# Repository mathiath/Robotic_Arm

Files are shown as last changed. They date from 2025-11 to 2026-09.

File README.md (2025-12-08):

# Robotic Arm – HiØ Anvendt Robotteknikk (Fall 2025)

Firmware and serial communication interface for a 6-DOF robotic arm developed for the Applied Robotics course at Høgskolen i Østfold.

This code runs on a Teensy 4.1 and communicates with RoboDK through a Python bridge.

---

## Installing the Firmware
1. Install Arduino IDE.
2. Use the following instructions to add the Teensy 4.1 board to Arduino IDE: https://www.pjrc.com/teensy/td_download.html
3. Open `main.ino` in the Arduino IDE.
4. Select **Teensy 4.1** under Tools - Board.
5. Upload.

The file `serial.ino` is automatically detected and compiled by Arduino.

---

## Basic Usage

### 1. Startup Procedure

To ensure correct homing and encoder alignment:

1. Place the robot in the upright zero position (all joints at 0°)
2. Insert zeroing pins
3. Power the motor drivers
4. Connect USB to the Teensy, and wait for it to initialize and calibrate
5. Remove the pins before any movement is executed

### 2. Home Button

Pressing the HOME button moves the robot to the zero position for all joints.

### 3. FreeMove Mode

- The FreeMove button toggles the motor power.
- When FreeMove is active:
  - Motors are disabled.
  - The arm can be moved freely by hand, while still sending encoder-data to RoboDK

### 4. Serial Control

The controller accepts the following commands:

- `R[...]`  – set joint targets  
- `L<number>` – set robot speed  
- `E` – return current joint values  
- `G0` / `G1` – gripper off/on

---

## Emergency Stop (E-STOP)

- Pressing the E-STOP button immediately disables all motors. 
- The arm may fall freely depending on payload and joint position.

The E-STOP is a latching, dual-circuit safety stop:
- One circuit physically cuts the stepper driver ENABLE lines.
- The other provides a firmware-level stop for redundancy, and allows for future digital feedback to RoboDK.

The arm will not be operational until the E-STOP is manually unlatched and the system has been power-cycled and re-homed.

### Reset Procedure
1. Unplug the power to the arm and disconnect the USB cable
2. Unlatch the E-STOP button
3. Place the robot in the upright zero position
4. Insert zeroing pins
5. Reconnect motor power
6. Reconnect USB to the Teensy and wait for it to initialize and calibrate
7. Remove the pins before any movement is executed

---

## File Overview

- `main.ino` - Firmware: stepping, encoders, safety, button handling
- `serial.ino` - Serial parser used for RoboDK/Python communication 

Both files are compiled automatically by the Arduino IDE.

---

## Notes

- Current setup uses a single shared speed value for all joints, due to the RoboDK - Python interface.
- Acceleration smoothing is not implemented in this version.

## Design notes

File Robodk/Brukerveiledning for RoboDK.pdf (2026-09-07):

Brukerveiledning for RoboDK

Import av robotobjekt
For å sette opp simulering og etablere kommunikasjon mellom RoboDK og den fysiske roboten, må robotmodellen først legges inn i prosjektfilen. Dette gjøres ved å åpne RoboDK og utføre følgende:
1. Åpne en RoboDK-fil.
2. Gå til File → Open.
3. Velg robotmodellen av kalt: My-Mechanism.

Når robotobjektet er importert, må det konfigureres slik at alle parametere samsvarer med robotens virkelige spesifikasjoner.

Konfigurering av roboten
Høyreklikk på robotobjektet i RoboDK og velg Modify Robot.
Et nytt vindu åpnes, der alle innstillinger skal settes slik som angitt i referansebildet. Disse parameterne må stemme overens med robotens mekaniske og kinematiske data for at simuleringen skal være nøyaktig.

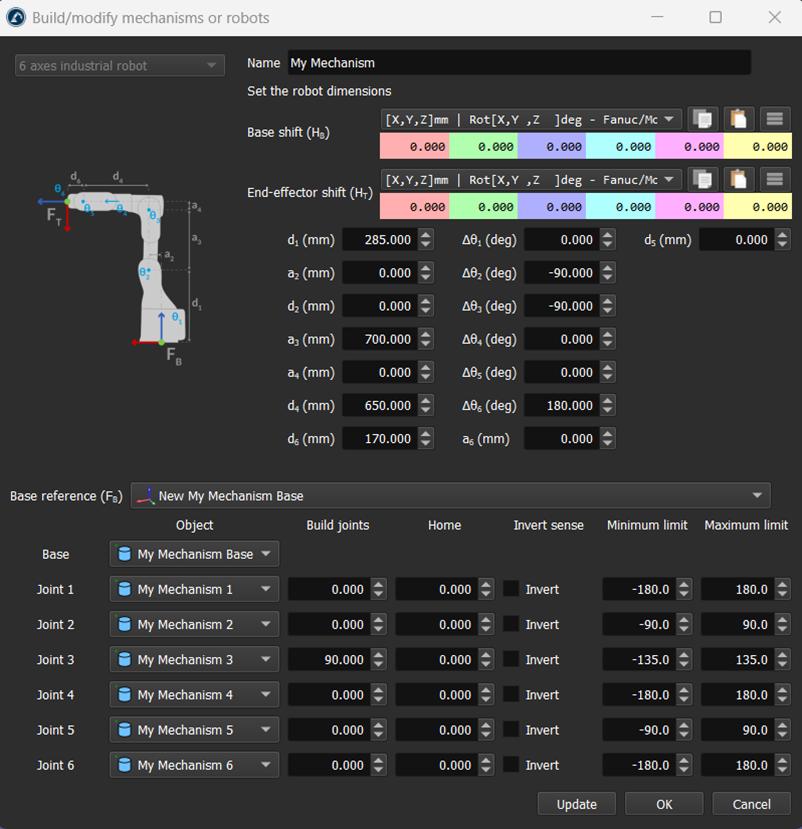
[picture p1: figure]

Når alle innstillinger samsvarer med spesifikasjonen, trykk Update og deretter OK.

Brukerveiledning for RoboDK

Plassering av robotbiblioteket
For at RoboDK skal kunne kommunisere med robotens bibliotek, må bibliotekfilen ligge i datamaskinens Temp-mappe. Dette kan gjøres på flere måter, men følgende metode er et effektivt alternativ (for Windows):
1. Opprett et nytt Python-script i RoboDK ved å høyreklikke i prosjektet og velge Add Python Script.
2. Høyreklikk deretter på scriptet og velg Edit Python Script.
3. I scriptvinduet, gå til File → Open/Open file.
4. RoboDK åpner da automatisk Temp-mappen på PC-en.
5. Legg robotbibliotekets fil i denne mappen.
Når biblioteket er plassert riktig, kan det brukes direkte av Python-skriptet.

Oppsett av Python-script for kommunikasjon
For å etablere kommunikasjon mellom roboten og RoboDK via Python, må klassen fra robotbiblioteket importeres.
Øverst i scriptet må følgende være definert:
- Import av robotens bibliotekklasse
- Opprettelse av et objekt av denne klassen
Dette objektet gjør det mulig å sende kommandoer og hente status fra roboten. Bilde under vise en eksempel kode som demonstrer bruken av objektet.

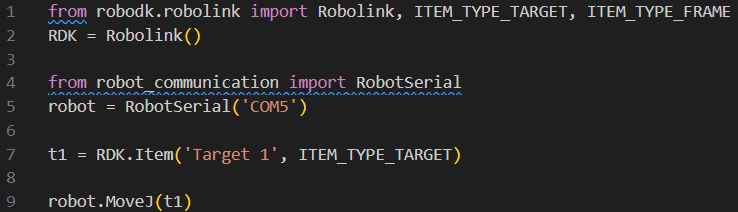
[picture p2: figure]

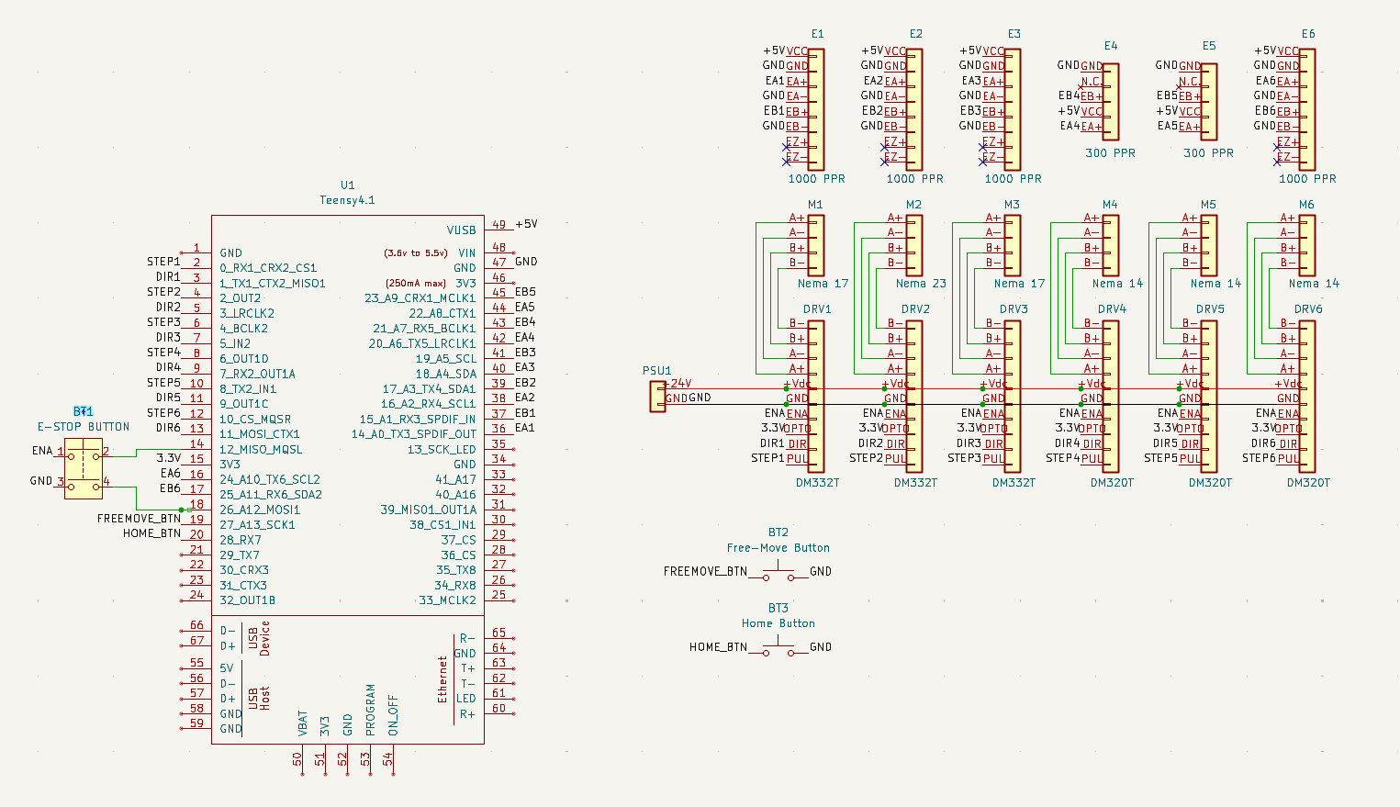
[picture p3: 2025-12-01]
schematic/robot_schematic.png

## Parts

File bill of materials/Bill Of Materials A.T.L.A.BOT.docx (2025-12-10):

# Bill Of Materials

PA12-GF15: ca 2,5kg uten feil.

https://polyalkemi.no/fiberlogy/101416/fiberlogy-nylon-pa12-plus-gf15-red

https://polyalkemi.no/fiberlogy/101413/fiberlogy-nylon-pa12-plus-gf15-black

PLA (for låsepinner)

da trenger vi også en hardened nozzle for å ikke ødelegge maskinen:

https://polyalkemi.no/bambu-lab/fah001-n-1/bambu-lab-hotend-for-p1-x1-hardened-steel-04mm

Tannhjul:

OBS, viktig med riktig dimensjoner og antall.

https://www.aliexpress.com/item/1005007667696756.html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

4x 20 teeth, 8mm bore

2x 28 teeth, 8mm bore

1x 40 teeth, 8mm bore

1x 30 teeth, 14mm bore

1x 40 teeth, 14mm bore

Encoderkabel:

CAT6 for encoder, skjermet, flerleder for fleksibilitet, 1stk.

https://www.avxperten.no/pds-kabel/s-ftp-cat6-bloed-100m-udendoers.asp

Kontakt for gripper: 1stk av hver

https://no.rs-online.com/web/p/industrial-circular-connectors/2088105

https://no.rs-online.com/web/p/sensor-actuator-cables/8566422

Mikrocontroller:

Teensy 4.1: https://www.amazon.com/gp/product/B08CTM3279?smid=A1283MCABFXB0Q&psc=1

Breakout board, screw mount: https://www.amazon.com/gp/product/B08R7P8G9X?smid=A2OVMUS055KMW5&psc=1

Hardware:

Diverse M3, M4, M5 og M6 maskinskruer, skiver og muttere

Ca 1m med 20x20 aluminiumsprofil gjerne av god kvalitet (stiv)

3mm svart MDF plate for kontrollerboks

Svart kabelsleeving

Tilfeldig bord fra skolen (med tillatelse)

Diverse strips

Kulelager:

Flatlager, 2stk:

https://www.123bearing.eu/bearing-housing/needle-roller-bearing/axial-needle/axk6085

Mellomstore lager, 4stk:

https://www.123bearing.eu/bearing-housing/deep-groove-bearing/single-row/61812-zz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

Store lager til base, 1stk:

https://www.123bearing.eu/bearing-housing/deep-groove-bearing/single-row/61928-2rs

Steppermotorer og girkasser:

1x https://www.omc-stepperonline.com/nema-17-closed-loop-stepper-motor-45ncm-64oz-in-with-magnetic-encoder-1000ppr-4000cpr-17hs15-1504-me1k

1x https://www.omc-stepperonline.com/eg-series-planetary-gearbox-gear-ratio-10-1-backlash-15-arc-min-for-nema-17-stepper-motor-eg17-g10

1x https://www.omc-stepperonline.com/nema-23-closed-loop-stepper-motor-1-20nm-169-93oz-in-with-magnetic-encoder-1000ppr-4000cpr-23hs22-4004-me1k

1x https://www.omc-stepperonline.com/eg-series-planetary-gearbox-gear-ratio-50-1-backlash-20-arc-min-for-6-35mm-shaft-nema-23-stepper-motor-eg23-g50-d6

1x https://www.omc-stepperonline.com/nema-17-closed-loop-stepper-motor-65ncm-92oz-in-with-magnetic-encoder-1000ppr-4000cpr-17hs24-2104-me1k

1x https://www.omc-stepperonline.com/eg-series-planetary-gearbox-gear-ratio-20-1-backlash-20-arc-min-for-nema-17-stepper-motor-eg17-g20

1x https://www.omc-stepperonline.com/nema-14-closed-loop-stepper-motor-40ncm-56-7oz-in-encoder-300cpr-14hs20-1504d-e22-300

3x https://www.omc-stepperonline.com/eg-series-planetary-gearbox-gear-ratio-20-1-backlash-20arc-min-for-nema-14-stepper-motor-egs14-g20

1x https://www.omc-stepperonline.com/nema-14-closed-loop-stepper-motor-18ncm-25-5oz-in-encoder-300cpr-14hs13-0804d-e22-300

1x https://www.omc-stepperonline.com/nema-14-closed-loop-stepper-motor-12-5ncm-17-73oz-in-with-magnetic-encoder-1000ppr-4000cpr-14hs11-1004-me1k

Stepper drivere:

4x (1 backup) https://www.omc-stepperonline.com/digital-stepper-drive-1-0-3-2a-18-30vdc-for-nema-17-23-stepper-motor-dm332t

4x (1 backup) https://www.omc-stepperonline.com/digital-stepper-driver-0-3-2-2a-10-30vdc-for-nema-8-11-14-16-17-stepper-motor-dm320t

Strømforsyning:

1x https://www.omc-stepperonline.com/400w-24v-16-7a-115-230v-switching-power-supply-stepper-motor-cnc-router-kits-s-400-24

Motorkabel:

15m: https://www.omc-stepperonline.com/awg-20-high-flexible-with-shield-layer-stepper-motor-cable-cm-20s

Elektriske småkomponenter:

Diverse jumper kabler

Wago klammer

2stk pushbuttons for homing og freemove

1stk låsende bryter for nødstopp

C13 apparatledning.

Micro-usb kabel

1x sikret bryter for 230v

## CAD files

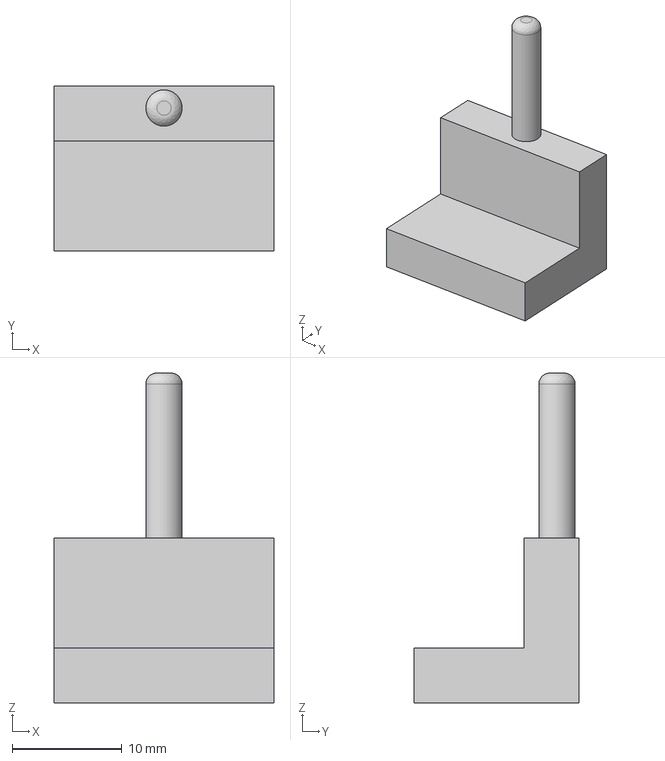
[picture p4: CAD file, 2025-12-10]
3D Models/locking_pin_joint6.step
20.0 x 15.0 x 30.0 mm

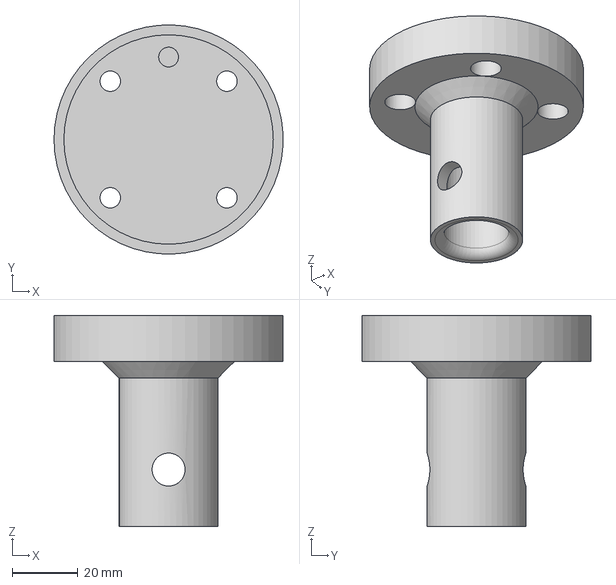
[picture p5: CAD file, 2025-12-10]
3D Models/tool_penholder.step
69.4 x 69.5 x 64.0 mm

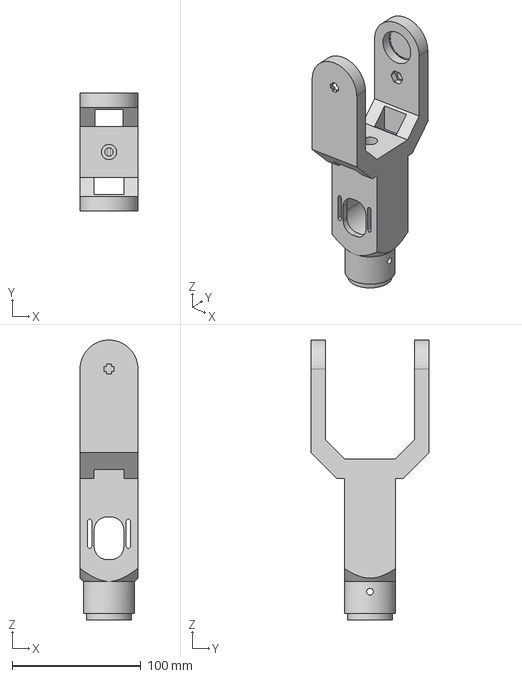
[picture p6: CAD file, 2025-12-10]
3D Models/fork_joint5_6.step
45.0 x 91.8 x 217.5 mm

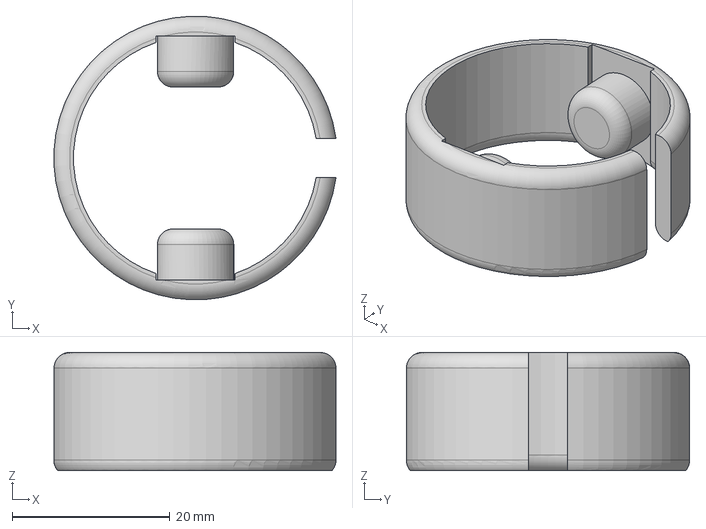
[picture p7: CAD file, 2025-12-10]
3D Models/tool_penholder_pressure_ring.step
35.8 x 36.0 x 15.0 mm

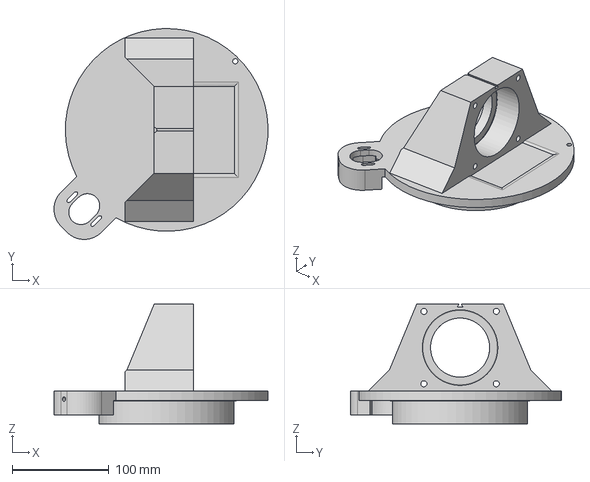
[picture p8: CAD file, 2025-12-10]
3D Models/base_top.step
221.7 x 218.4 x 124.0 mm

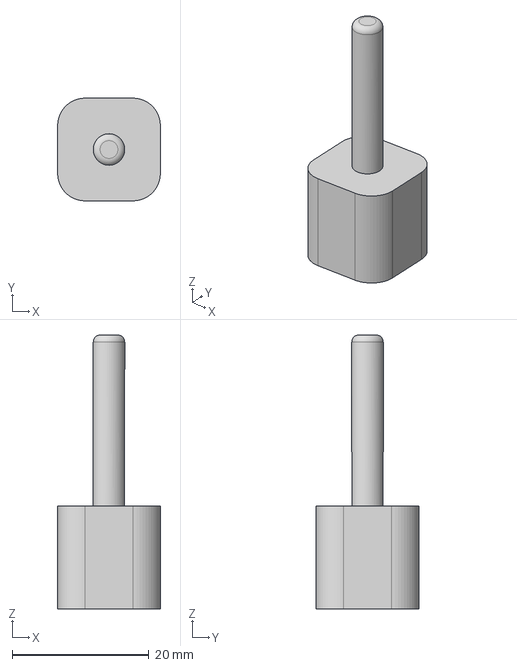
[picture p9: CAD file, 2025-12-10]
3D Models/locking_pin_joint1.step
15.0 x 15.0 x 40.0 mm

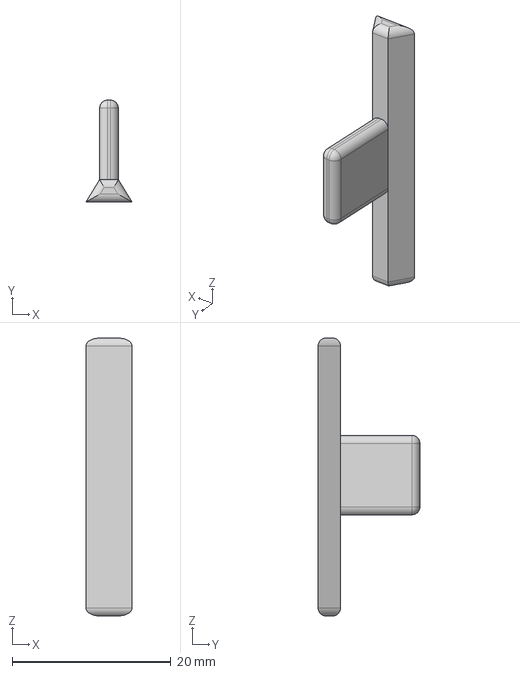
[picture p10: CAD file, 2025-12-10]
3D Models/locking_pin_joint2_3_4_might_need_some_scaling.step
5.80 x 12.8 x 35.0 mm

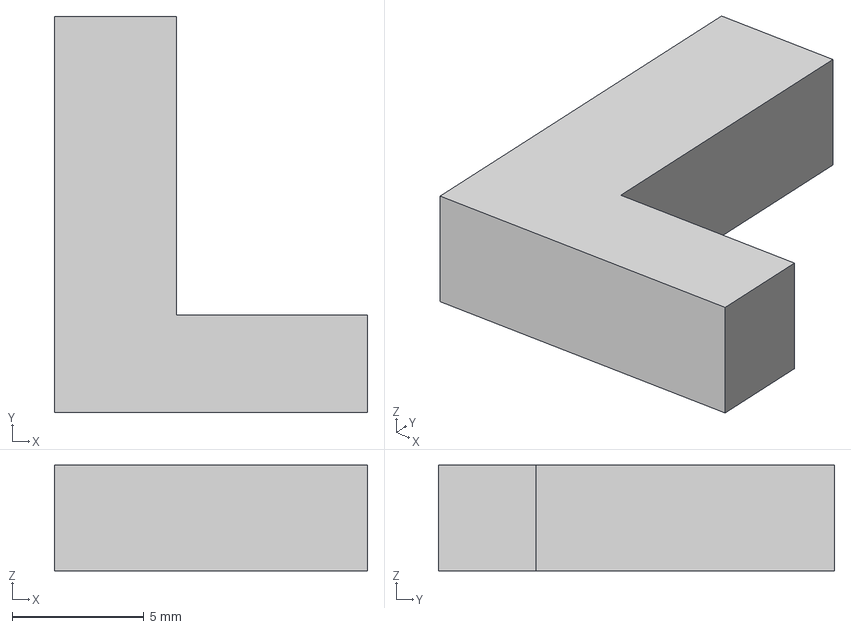
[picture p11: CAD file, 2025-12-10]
3D Models/letter_L.step
11.9 x 15.0 x 4.00 mm

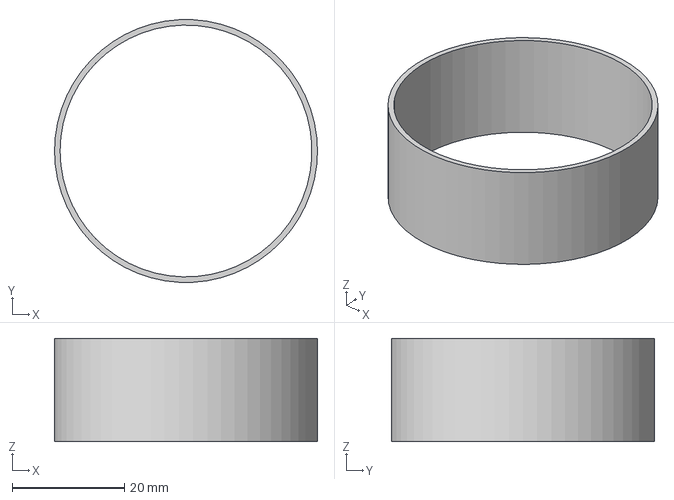
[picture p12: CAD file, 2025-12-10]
3D Models/joint4_middle_bearing_spacer.step
46.9 x 46.8 x 18.4 mm

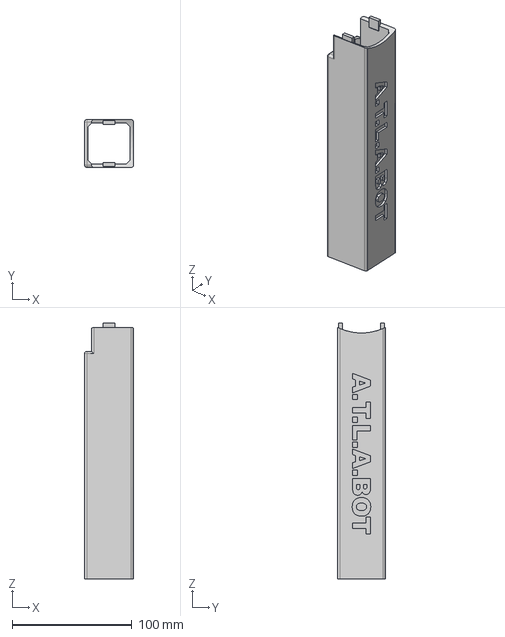
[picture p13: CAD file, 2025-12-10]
3D Models/upper_shroud_joint2-3.step
41.0 x 40.0 x 213.6 mm

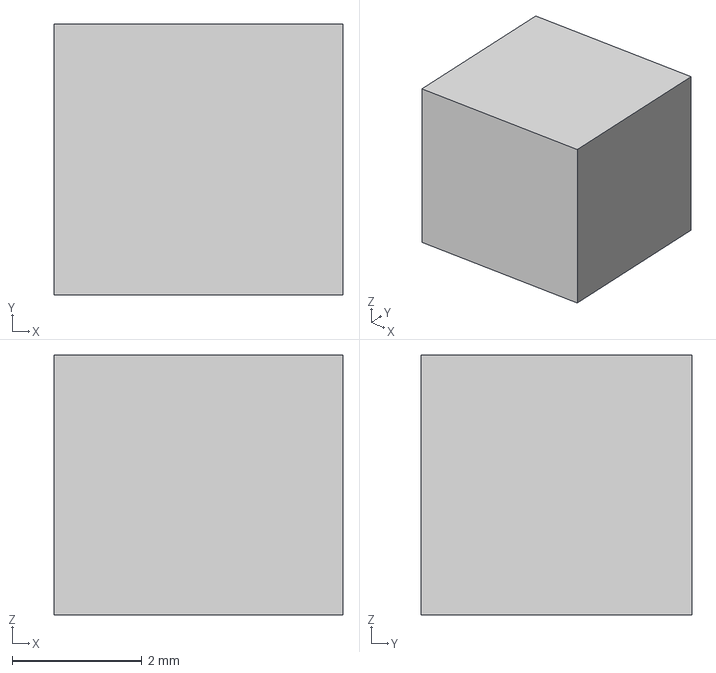
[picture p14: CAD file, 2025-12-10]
3D Models/letter_dot.step
4.45 x 4.17 x 4.00 mm

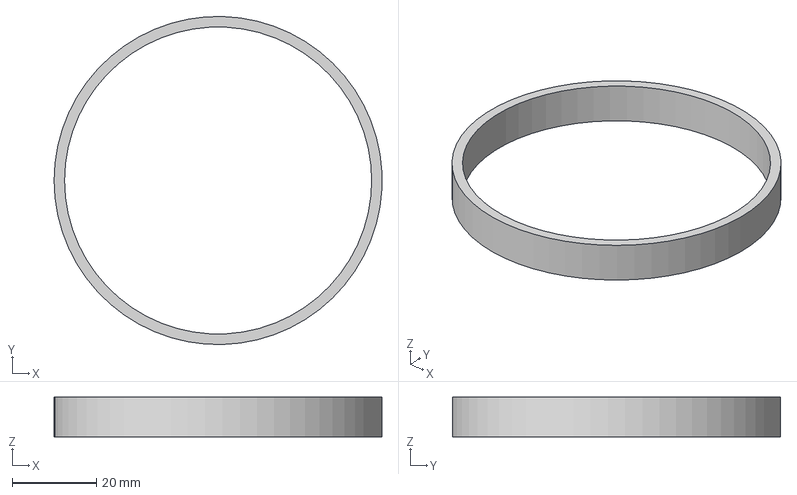
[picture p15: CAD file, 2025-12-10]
3D Models/joint2_3_bearing_spacer.step
77.9 x 78.0 x 9.50 mm

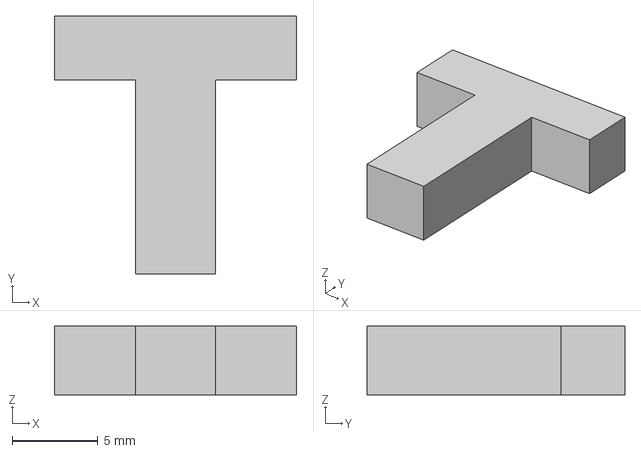
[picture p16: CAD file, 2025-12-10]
3D Models/letter_T.step
14.1 x 15.0 x 4.00 mm

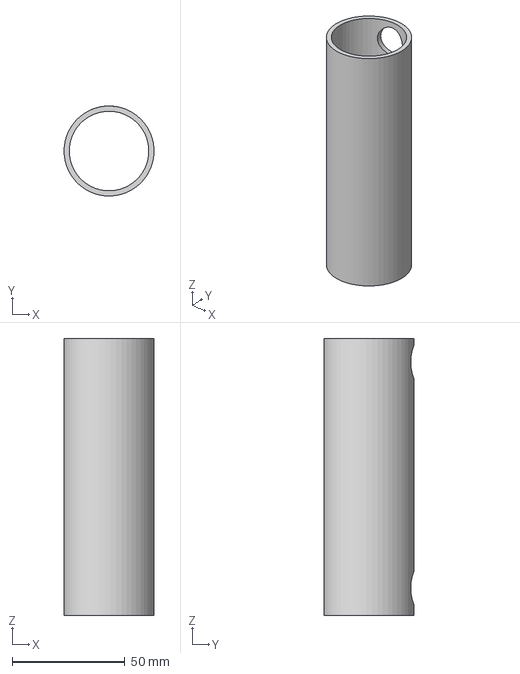
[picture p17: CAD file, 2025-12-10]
3D Models/upper_shroud_joint4_5.step
40.0 x 40.0 x 123.0 mm

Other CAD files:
3D Models/joint4_inner.step
3D Models/letter_A.step
3D Models/letter_B.step
3D Models/joint5_spacer.step
3D Models/CNC_cut_belt_pulley_T5_10T.f3d
3D Models/Elektronikkboks.f3d
3D Models/base_bottom.step
3D Models/joint2_inner.step
3D Models/joint2_motor_plate.step
3D Models/joint3_4_inner.step
3D Models/joint3_motor_plate.step
3D Models/joint3_outer.step
3D Models/joint4_outer_bearing_spacer_2pc.step
3D Models/joint5_6_housing.step
3D Models/joint6_outer.step
3D Models/letter_O.step
3D Models/locking_pin_joint5.step

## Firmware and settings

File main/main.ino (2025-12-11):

/* 
    Inspired by AR4 Robot Control Software
    Copyright (c) 2024, Chris Annin
    All rights reserved.

    This revision of the code has a shared speed for all joints during movement, due to the current RoboDK configuration only delivering one speed variable.

    To do: update gear ratios
*/

#include <Arduino.h>
#include <math.h>
#include <Encoder.h>

const int n_J = 6; // Number of joints

// external variables from RoboDK interface
extern float Jlist[6];
extern int robot_speed; // % of joint max deg/s

// pins
const int stepPin[n_J] = {0, 2, 4, 6, 8, 10};
const int dirPin[n_J]  = {1, 3, 5, 7, 9, 11};

const int encAPin[n_J] = {14, 16, 18, 20, 22, 24};
const int encBPin[n_J] = {15, 17, 19, 21, 23, 25};

const int enPin      = 12;
const int eStopPin   = 26; // latching button
const int freeMovePin= 27; // momentary button, yellow
const int homePin    = 28; // momentary button, green

// motor + encoder + driver specs
const int SPR = 1600; // motor steps per rev
const int CPR[n_J]       = {4000, 4000, 4000, 1200, 1200, 4000}; // encoder counts per rev
const float gearRatio[n_J] = {71,   50,   20,   20,   33.333,   20};   // gearbox ratio

const int invDir[n_J] = {0, 0, 0, 0, 0, 0}; // invert direction for motors

// encoder instances (one per joint)
Encoder enc[n_J] = {
    Encoder(encAPin[0], encBPin[0]),
    Encoder(encAPin[1], encBPin[1]),
    Encoder(encAPin[2], encBPin[2]),
    Encoder(encAPin[3], encBPin[3]),
    Encoder(encAPin[4], encBPin[4]),
    Encoder(encAPin[5], encBPin[5]),
};

// Joint limits (deg)
float limPos[n_J] = {180.0f,  90.0f,  135.0f, 360.0f,  90.0f,  360.0f};
float limNeg[n_J] = {-180.0f, -90.0f, -135.0f, -360.0f, -90.0f, -360.0f};

// Maximum velocity per joint (deg/s at 100% speed)
const float maxSpeed[n_J] = {30.0f, 20.0f, 30.0f, 40.0f, 30.0f, 180.0f};

const float accelK = 0.2f; // Acceleration duration (% of movement)
const float accelMinSpeed = 0.2f; // Percentage of speed at the acceleration's slowest point.

// internal vars
float encMult[n_J];  // encoder counts per degree (includes gearbox)
float stepDeg[n_J];  // motor steps per degree (includes gearbox)
long  encRaw[n_J];   // raw encoder counts
float encDeg[n_J];   // encoder deg position

long  stepCount[n_J]; // accumulated step count
float jointDeg[n_J];  // current joint angle (deg) from step count
long totalSteps[n_J]; // total steps for current move (for accel/decel)
long stepsDone[n_J];  // steps already taken in current move

// function state flags
bool motorsEnabled   = false;
bool eStopEnabled    = false;
bool freeMoveEnabled = false;

// init step/dir pins
void initPins() {
    pinMode(enPin, OUTPUT);
    pinMode(eStopPin, INPUT_PULLUP);
    pinMode(freeMovePin, INPUT_PULLUP);
    pinMode(homePin, INPUT_PULLUP);

    digitalWrite(enPin, LOW); // disable motors at startup
    
    // init all motor pins
    for (int j = 0; j < n_J; j++) {
        pinMode(stepPin[j], OUTPUT);
        pinMode(dirPin[j],  OUTPUT);
        digitalWrite(stepPin[j], LOW);
        digitalWrite(dirPin[j],  LOW);
    }
}

// init conversion parameters
void initParams() {
    for (int j = 0; j < n_J; j++) {
        encMult[j] = (float)(CPR[j] * gearRatio[j]) / 360.0f;
        stepDeg[j] = (float)(SPR   * gearRatio[j]) / 360.0f;
    }
}

// enable / disable motor drivers
void enableMotors(bool on) {
    motorsEnabled = on;
    digitalWrite(enPin, on ? HIGH : LOW);
}

// convert degrees to motor steps
long degToSteps(int joint, float deg) {
    if (joint < 0 || joint >= n_J) return 0;
    return lroundf(deg * stepDeg[joint]);
}

// convert motor steps to degrees
float stepsToDeg(int joint, long steps) {
    if (joint < 0 || joint >= n_J) return 0.0f;
    return (float)steps / stepDeg[joint];
}

// update encoder readings (1 kHz max rate)
void updateEncoders() {
    static unsigned long lastUpdate = 0;
    const unsigned long interval = 1000;
    unsigned long now = micros();
    
    if (now - lastUpdate >= interval) {
        lastUpdate = now;

        for (int j = 0; j < n_J; j++) {
            encRaw[j] = enc[j].read();
            encDeg[j] = (float)encRaw[j] / encMult[j];
        }
    } 
}

// main joint motion function
void moveJointsToDeg(const float targetDeg[n_J], float speed = 25.0f) {
    // abort if unsafe
    if (!motorsEnabled || eStopEnabled || freeMoveEnabled) return;

    long  remSteps[n_J];
    int   direction[n_J];
    unsigned long stepIntervalUs[n_J];
    unsigned long lastStepUs[n_J];
    bool  stepLevel[n_J];

    bool hasActiveJoint = false;
    unsigned long nowUs = micros();

    // preprocess targets
    for (int j = 0; j < n_J; j++) {

        float deg = targetDeg[j];

        // limit angle to joint range
        if (deg > limPos[j]) deg = limPos[j];
        if (deg < limNeg[j]) deg = limNeg[j];

        // global speed = prosent (0–100) av maxSpeed for hvert ledd
        float speedK = speed;
        if (speedK < 0.0f)  speedK = 0.0f;
        if (speedK > 100.0f) speedK = 100.0f;

        float jointSpeed = maxSpeed[j] * (speedK / 100.0f);
        // sikkerhet: ikke negativ
        if (jointSpeed < 0.0f) jointSpeed = 0.0f;

        // calculate step difference
        long delta = degToSteps(j, deg) - stepCount[j];
        remSteps[j] = labs(delta);
        totalSteps[j] = remSteps[j];
        stepsDone[j] = 0;

        // skip if no motion needed
        if (remSteps[j] == 0 || jointSpeed == 0.0f) {
            stepIntervalUs[j] = 0;
            continue;
        }

        hasActiveJoint = true;

        // set direction pin
        direction[j] = (delta >= 0) ? 1 : -1;

        bool dirPinState = (direction[j] > 0);
        if (invDir[j]) dirPinState = !dirPinState;
        digitalWrite(dirPin[j], dirPinState ? HIGH : LOW);

        // convert deg/s to steps/s to microsecond step interval
        float stepsPerSec = jointSpeed * stepDeg[j];
        if (stepsPerSec < 1.0f) stepsPerSec = 1.0f;

        stepIntervalUs[j] = (unsigned long)(1000000.0f / (2 * stepsPerSec));
        lastStepUs[j] = nowUs;

        stepLevel[j] = LOW;
        digitalWrite(stepPin[j], LOW);
    }

    if (!hasActiveJoint) return;

    // stepping loop (blocking)
    while (true) {
        handleEStop();
        handleFreeMove();

        // Immediately stop motion if unsafe condition is active
        if (eStopEnabled || freeMoveEnabled) break;
            
        unsigned long now = micros();
        bool moving = false;

        for (int j = 0; j < n_J; j++) {
            // Skip joints that are finished or inactive
            if (remSteps[j] == 0 || stepIntervalUs[j] == 0) continue;

            // Base step interval (cruise)
            unsigned long intervalUs = stepIntervalUs[j];

            // Simple accel/decel profile based on progress (0..1)
            if (totalSteps[j] > 0) {
                float pos   = (float)stepsDone[j] / (float)totalSteps[j]; // 0..1
                float scale = 1.0f;

                if (pos < accelK) {
                    // Acceleration phase (start)
                    float t = pos / accelK; // 0 -> 1
                    scale = accelMinSpeed + (1.0f - accelMinSpeed) * t;
                } else if (pos > 1.0f - accelK) {
                    // Deceleration phase (end)
                    float t = (1.0f - pos) / accelK; // 0 -> 1 towards the end
                    scale = accelMinSpeed + (1.0f - accelMinSpeed) * t;
                } else {
                    // Cruise phase
                    scale = 1.0f;
                }

                // Higher scale = higher speed = shorter interval
                intervalUs = (unsigned long)((float)stepIntervalUs[j] / scale);
            }

            // Time to toggle step pin?
            if (now - lastStepUs[j] >= intervalUs) {
                lastStepUs[j] += intervalUs;

                // Toggle step signal
                stepLevel[j] = !stepLevel[j];
                digitalWrite(stepPin[j], stepLevel[j]);

                // Count steps only on falling edge
                if (stepLevel[j] == LOW) {
                    remSteps[j]--;
                    stepsDone[j]++;               // track progress for accel/decel
                    stepCount[j] += direction[j];
                    jointDeg[j]  = stepsToDeg(j, stepCount[j]);
                }
            }

            // If any joint still has remaining steps, keep loop running
            if (remSteps[j] > 0) moving = true;
        }

        // Exit loop when all joints are finished
        if (!moving) break;
    }


}

// reset all positions to zero
void setHome() {
    if (eStopEnabled) return;

    for (int j = 0; j < n_J; j++) {
        enc[j].write(0);
        encRaw[j]  = 0;
        encDeg[j]  = 0.0f;
        stepCount[j] = 0;
        jointDeg[j]  = 0.0f;
    }
}

// move robot to home position (0 deg all joints, straight up)
void moveHome(float speed = 50.0f) {
    float targetDeg[n_J] = {0, 0, 0, 0, 0, 0};
    moveJointsToDeg(targetDeg, speed);
}

// debounced e-stop handler
void handleEStop() {
    static bool lastRaw = HIGH;
    static bool lastStable = HIGH;
    static unsigned long lastDebounce = 0;
    const unsigned long debounceDelay = 50; // ms

    static unsigned long lastPrint = 0;
    const unsigned long printDelay = 200;

    bool raw = digitalRead(eStopPin);
    unsigned long now = millis();

    if (raw != lastRaw) {
        lastDebounce = now;
        lastRaw = raw;
    }

    if ((now - lastDebounce) > debounceDelay) {
        if (raw != lastStable) {
            lastStable = raw;

            if (raw == LOW) {
                eStopEnabled = true;
                enableMotors(false);
                Serial.println("ESTOP ENABLED");
            }
        }     
    }

    if (eStopEnabled) {
        if (now - lastPrint >= printDelay) {
            lastPrint = now;
            Serial.println("ESTOP ENABLED");
        }
    }
}

// debounced free-move toggle
void handleFreeMove() {
    static bool lastRaw = HIGH;
    static bool lastStable = HIGH;
    static unsigned long lastDebounce = 0;
    const unsigned long debounceDelay = 50; // ms    

    bool raw = digitalRead(freeMovePin);
    unsigned long now = millis();

    if (raw != lastRaw) {
        lastDebounce = now;
        lastRaw = raw;
    }

    if ((now - lastDebounce) > debounceDelay) {
        if (raw != lastStable) {
            lastStable = raw;

            if (raw == LOW) {
                if (eStopEnabled) {
                    Serial.println("FREEMOVE BLOCKED - ESTOP ACTIVE");
                    return;
                }

                freeMoveEnabled = !freeMoveEnabled;
                enableMotors(!freeMoveEnabled);
                Serial.println(freeMoveEnabled ? "FREEMOVE ON" : "FREEMOVE OFF");
            }
        }
    }
}

// debounced home button
void handleHome() { 
    static bool lastVal = HIGH;
    static unsigned long lastTime = 0;
    const unsigned long debounceDelay = 50; // ms

    bool raw = digitalRead(homePin);
    unsigned long now = millis();

    if (now - lastTime > debounceDelay) {
        if (raw == LOW && lastVal == HIGH) {
            if (!eStopEnabled && !freeMoveEnabled) {
                moveHome();
            }
        }
        lastVal = raw;
        lastTime = now;
    }
}

void setup() {
    Serial.begin(115200);
    initPins();
    initParams();
    setHome();
    enableMotors(true);
}

void loop() {
    updateEncoders();
    handleEStop();
    handleFreeMove();
    handleHome();

    if (eStopEnabled) return;

    // serial command handler
    if (Serial.available() > 0) {
        handleSerialInput();
        moveJointsToDeg(Jlist, (float)robot_speed);
        Serial.println("[" + String(Jlist[0]) + " " + String(Jlist[1]) + " " 
                           + String(Jlist[2]) + " " + String(Jlist[3]) + " "
                           + String(Jlist[4]) + " " + String(Jlist[5]) + "]");
        update_encoder_valus();
        Serial.println("end");
    }
}

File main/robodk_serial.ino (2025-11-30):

String encoder_value = "0.0,0.0,0.0,0.0,0.0,0.0"; //Encoder data
int robot_speed = 30;
int gripper_mode = 0;

String message = "0";
float Jlist[6] = {0.0, 0.0, 0.0, 0.0, 0.0, 0.0}; // a list of all joint angles in degrees

void update_encoder_valus() {
  encoder_value = String(Jlist[0]) + "," + String(Jlist[1]) + "," + String(Jlist[2]) + "," + String(Jlist[3]) + "," + String(Jlist[4]) + "," + String(Jlist[5]);
}

void handleSerialInput() {
  message = Serial.readStringUntil('\n');
  char type = message.charAt(0);
  message.remove(0,1);
  message.trim();
  String text;

  switch (type) {
    case 'R': //Degrees for all the joints
      listCheck(message);
      break;

    case 'S': //Speed for all the joints
      //return listCheck(message);
      break;

    case 'L': //Robot speed
      robot_speed = message.toInt();
      Serial.println(String("Robot speed is: ") + String(robot_speed));
      break;

    case 'E':
      Serial.println("Encoder:" + encoder_value);
      break;

    case 'G': // activeing gripper function
      gripper_mode = message.toInt();
      if (gripper_mode == 1) {
        Serial.println("Gripper is turned on");
      }
      else if (gripper_mode == 0) {
        Serial.println("Gripper is turned off");
      }
      break;

    default:
      Serial.println("Input not defined");
      break;
  }
}

void listCheck(String message) {
  if (message[0] != '[' || message[message.length() - 1] != ']') {
    Serial.println("List input not defined");
  }
  else if (message.indexOf('[',1) != -1) {
    for (int i=0; i <= message.length(); i++) {
      if (message.indexOf('[',1) != -1) {
        message.remove(0, message.indexOf('[',1));
      }
      else if (message[0] != '[' || message[message.length() - 1] != ']') {
        Serial.println("List input not defined");
      }
      else {
        dataInToList(message);
        break;
      }
    }
  }
  else {
  dataInToList(message);
  }
}

void dataInToList(String dataList) {
  //start utgangs punkt
  int i = dataList.indexOf('[');
  int k = 0;
  //itererer gjenomm listen
  while(i++>-1) {
    if (i > 43) {
      break;
    }
    //leser frem til den finner ',' . i er start punktet
    int j = dataList.indexOf(',',i); 
    //setter verdien i Jlist til det som er i mellom i og j
    Jlist[k++]= dataList.substring(i,j).toFloat();
    i = dataList.indexOf(',',j);
  } 
}

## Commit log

2025-11-23 accounting for 2:1 belt on J5
2025-11-26 initial commit, replaced PlatformIO with ino code
    [teensy.ino]
2025-11-27 arduino ide created folder
2025-11-27 added testing file for an indvidual joint
2025-11-29 implemented encoders, made a zeroing/homing + gohome function, improved movejointstodeg
2025-12-01 added schematic
    [hbot_schematic.kicad_pcb, hbot_schematic.kicad_sch]
2025-12-01 updated with hardware E-stop + software for redundancy. ujdpated readme, added schematic
    [hbot_schematic.kicad_sch]
2025-12-10 lagt til 3D modeller
    individuelle .STEP filer av alle deler og komlett fusion archive fil for hele prosjektet
    [CNC_cut_belt_pulley_T5_10T.f3d, base_bottom.step, base_top.step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]
2025-12-10 added acceleration curve to movement
    [hbot_schematic.kicad_pcb, hbot_schematic.kicad_sch]
2025-12-10 added electronics enclosure and stop button (elektronikkboks f3d)
    [Elektronikkboks.f3d]
2025-12-10 added bill of materials
2025-12-11 fixed home button
